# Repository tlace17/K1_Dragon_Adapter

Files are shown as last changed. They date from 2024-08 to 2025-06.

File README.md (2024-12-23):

# Getting Started:

This K1 printer mod is designed for intermediate users and requires my Linear Rail Gantry, along with some additional components. Once installed, it allows for extremely high flow rates of up to 50mm³/s and enables single-handed nozzle changes. You can choose between two setup options: the standard Volcano version and the MZE+V6 version. For most users, the Volcano version is preferable, as it delivers up to 80% of the maximum flow rates without needing special shrouds.

# What you need:

[BOM](https://docs.google.com/spreadsheets/d/1sPTMPV2eK_xJK3cMwCgg2oyzx_67ZIePCPmvhL2Yadw/)

[Adapter Plate](https://peedee3d.com/collections/k1/products/k1-series-g5-titanium-dragon-adaptor)

You also need a new printed carriage that can be found under the usermods section of the K1 Linear Rail Gantry [here](https://github.com/tlace17/K1-Linear-Rail-Gantry/tree/main/user-mods/BootyCall%20Jones/Dragon%20ACE%20Mod).

# Installation:

## Prepare heatsink:

1.) Drill through the heatsink heatbreak hole with 15/64” or 6mm drill bit:


2.) Using an M3x0.5mm tap, tap the holes circled below: 


3.) Attach the adapter plate to the bottom of the heatsink with 2 short M3 BHCS (4-8mm):


## Assemble hotend:

1.) Thread the heartbreak into the top of the hotend until ~1mm above flush:


2.) Insert the 4 ceramic standoffs into the hotend: 


3.) Apply Boron Nitride paste to the lower half of the smooth section of the heatbreak and insert it into the heatsink:


4.) Now, while holding the assembly together, carefully twist the top of the heatbreak with pliers or fingers to seat the threaded portion of the heartbreak as far into the hotend as possible (until you cannot spin anymore), this will ensure good seating of the ceramic standoffs.

5.) $${\color{red}This \space Step \space is \space Critical.}$$ Tighten the grub screw on the back of the heatsink and this should now have your hotend fully assembled. 

6.) Now fully thread and tighten your V6 Volcano or Volcano adapter+MZE+V6 into the hotend until it is fully seated, you will fully tighten this when hot.

## Wiring:

1.) Reterminate hotend and thermistor properly for the k1 toolhead and install your full hotend/heatsink assembly into the new printed carriage.

## Final Steps:

1.) Add the new length of PTFE between the heartbreak and the extruder and continue onto klipper to set up your new thermistor, tighten your nozzle while hot and run a new PID.

Happy printing

For additional assistance or to just hang out, [Join my Discord!](https://discord.gg/gRDr2ggNuM)

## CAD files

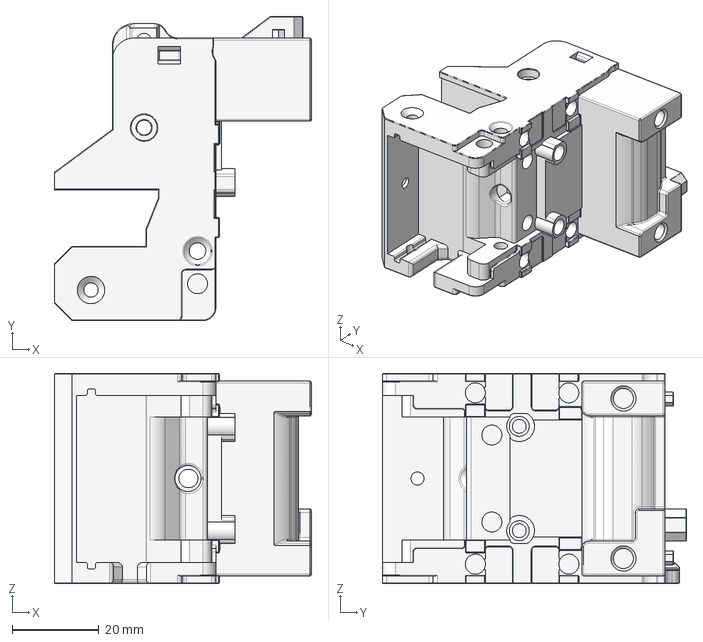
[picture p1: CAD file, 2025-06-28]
CAD/Linear Rail Carriage w Probe 4 ACE.step
59.1 x 70.0 x 48.4 mm

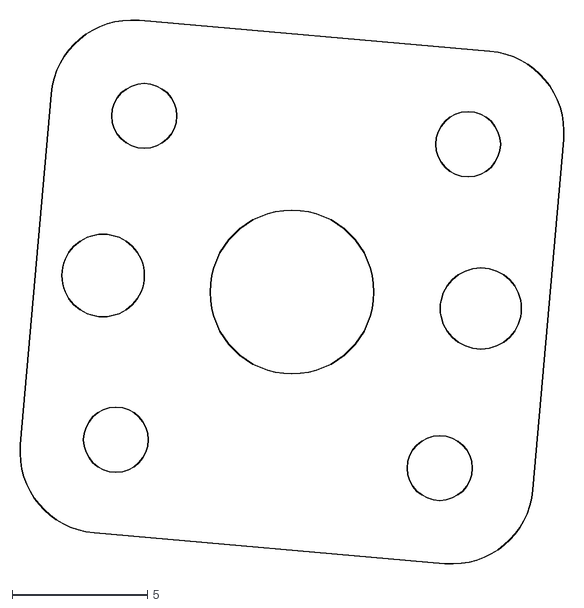
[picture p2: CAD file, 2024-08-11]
DXF/Dragon Adapter.dxf
20.3 x 20.3

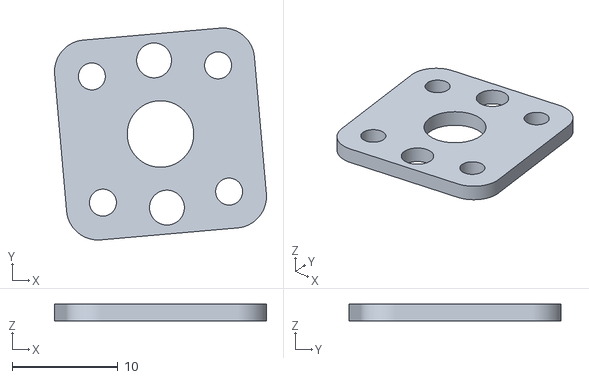
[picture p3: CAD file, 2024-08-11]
STL/Printable Adapter (high temp materials only).stl
20.1 x 20.1 x 1.59

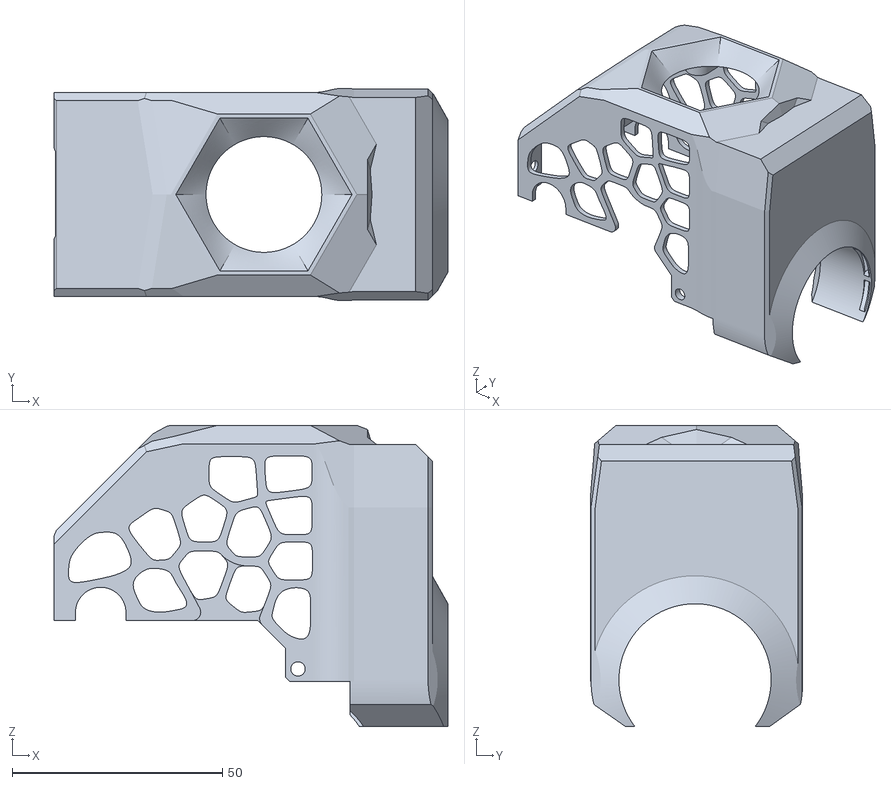
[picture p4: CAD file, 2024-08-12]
STL/Shrouds/BootyBurner for Dragon with MZE.stl
93.7 x 50.5 x 71.6

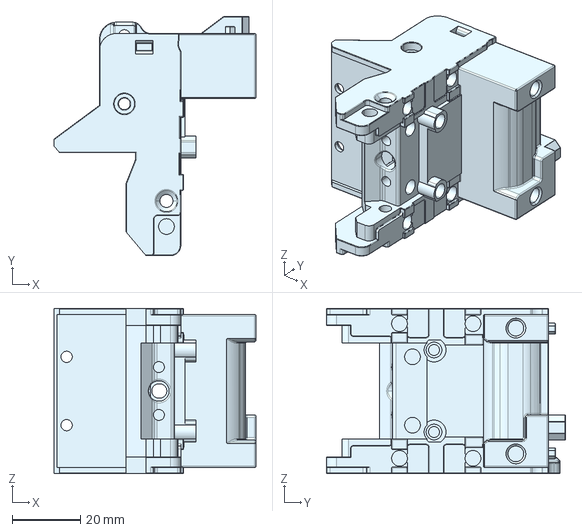
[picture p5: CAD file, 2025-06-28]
CAD/Linear Rail Carriage 4 ACE.step
59.1 x 70.0 x 48.4 mm

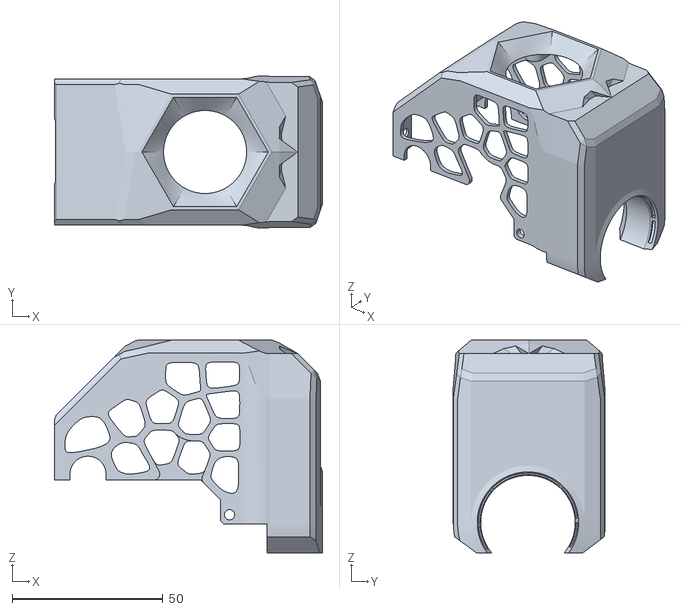
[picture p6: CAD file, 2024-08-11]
STL/Shrouds/BootyBurner for Dragon.stl
88.8 x 50.5 x 70.6

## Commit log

2024-08-11 New files
    [BootyBurner for Dragon ACE.stl, Dragon Adapter.dxf, Printable Adapter.stl]
2024-08-12 added shrouds
    [BootyBurner for Dragon with MZE.stl, BootyBurner for Dragon.stl]
2025-06-28 Add CAD
    [Linear Rail Carriage 4 ACE.step, Linear Rail Carriage w Probe 4 ACE.step]
